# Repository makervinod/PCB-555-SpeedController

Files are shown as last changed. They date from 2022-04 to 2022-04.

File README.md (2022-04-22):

# 555 Speed Controller

## A 555 Timer-based Speed Controller for controlling DC Speed/Dimming

<br>

> This speed controller was purposely built for controlling the speed of Ender 3D Printer's Hotend Cooling Fan to help the hot-end support unofficial cooling fans. But it can be used for other purposes too! ( No limits to your use case! )

---

### Specifications:

- Operating Voltage: **12V to 24V**
- Maximum Output Current: **0.5 Amp (customizable)**

---

### Components Required:

| Sr. No. | Part Number/Name | Package  | Quantity | Description |
| --- | --- | --- | :---: | --- |
| 1 | NE555 | SOIC-8 | 1 | 555-Timer IC |
| 2 | 1N4742 | DO-41 | 1 | Diode (12V Zener, 1 Watt) |
| 3 | LL4148 (1N4148)  | MiniMELF | 2 | Diode |
| 4 | S8050 (J3Y) | SOT-23 | 1 | NPN Transistor |
| 5 | 22uF 50V | 1210 | 1 | Ceramic Capacitor |
| 6 | 0.1uF 16V | 0805 | 1 | Ceramic Capacitor |
| 7 | 0.01uF 16V | 0805 | 1 | Ceramic Capacitor |
| 8 | 560 Ω | 2512 | 2 | Resistor |
| 9 | 10 kΩ | 0805 | 1 | Resistor |
| 10 | 1 kΩ | 0805 | 1 | Resistor |
| 11 | 4.7 kΩ | 0805 | 1 | Resistor |
| 12 | 10 kΩ | Preset | 1 | Preset Potentiomenter |
| 13 | LED (Any color)  | 0805 | 1 | LED |

---

### Fabrication Notes:

1. This was built using the PCB Toner transfer process at home.
2. Use the `print` feature of KiCAD to print the PCB design according to your requirements.
3. I tinned the board using some normal solder wire & flux (budget-friendly)
4. Refer to the schematic to relate the placement of the components.

---

### Additional Notes:

> The circuit will dissipate high heat if operated beyond the specified rating. Choose an appropriate combination of the Zener diode & the heat-dissipating resistors to satisfy your requirements.

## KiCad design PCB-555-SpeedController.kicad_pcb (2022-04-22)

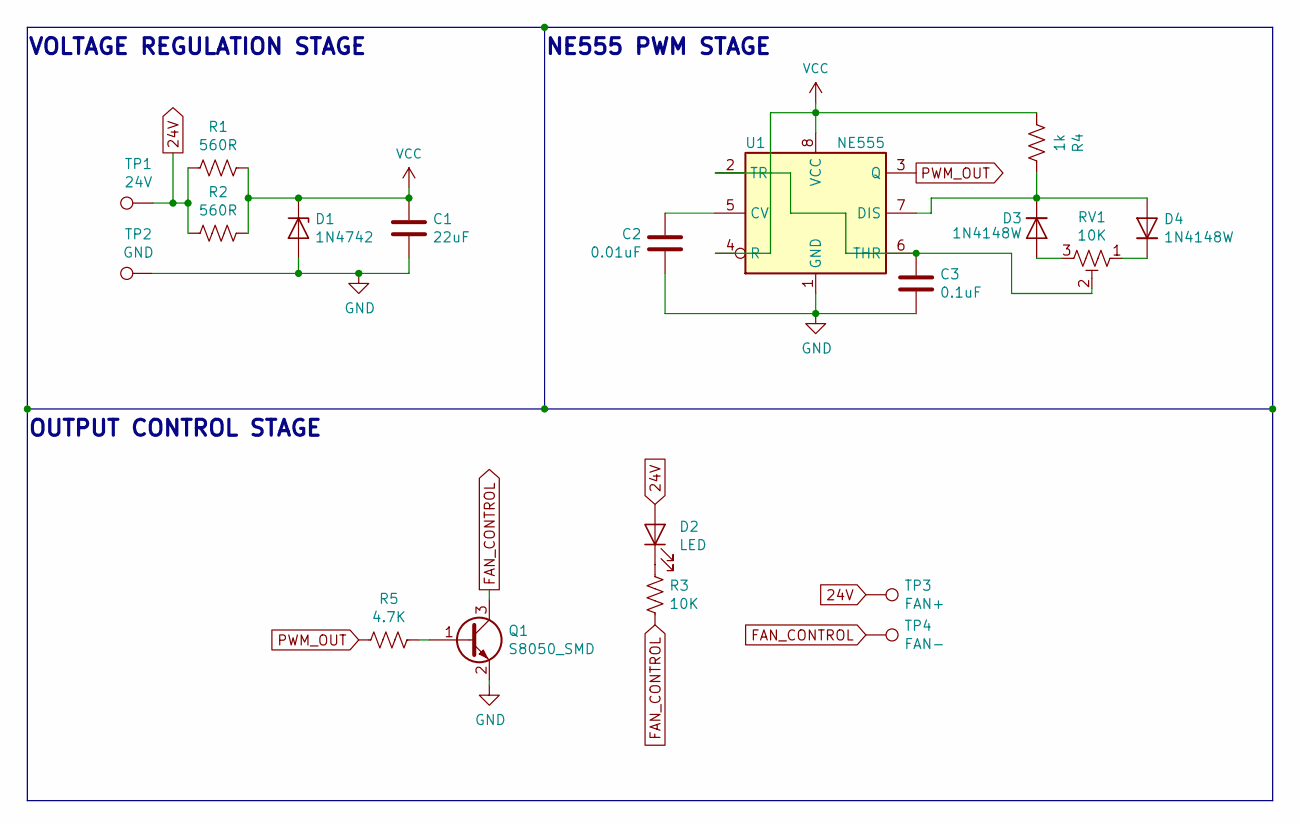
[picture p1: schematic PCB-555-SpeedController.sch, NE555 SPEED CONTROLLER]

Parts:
C1: 22uF; C_1210_3225Metric
C2: 0.01uF; C_0805_2012Metric
C3: 0.1uF; C_0805_2012Metric
D1: 1N4742; D_DO-41_SOD81_P10.16mm_Horizontal
D2: LED; LED_0805_2012Metric
D3, D4: 1N4148W; D_MiniMELF
Q1: S8050_SMD; SOT-23
R1, R2: 560R; R_2512_6332Metric
R3: 10K; R_0805_2012Metric
R4: 1k; R_0805_2012Metric
R5: 4.7K; R_0805_2012Metric
RV1: 10K; Potentiometer_Piher_PT-6-V_Vertical
TP1: 24V; TestPoint_Pad_2.0x2.0mm
TP2: GND; TestPoint_Pad_2.0x2.0mm
TP3: FAN+; TestPoint_Pad_2.0x2.0mm
TP4: FAN-; TestPoint_Pad_2.0x2.0mm
U1: NE555; SOIC-8_3.9x4.9mm_P1.27mm

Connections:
24V: D2.2 (A), R1.2, R2.2, TP1.1, TP3.1
FAN_CONTROL: Q1.3 (C), R3.1, TP4.1
GND: C1.2, C2.1, C3.2, D1.2 (A), Q1.2 (E), TP2.1, U1.1 (GND)
unnamed: C2.2, U1.5 (CV)
unnamed: C3.1, RV1.2, U1.2 (TR), U1.6 (THR)
unnamed: D2.1 (K), R3.2
unnamed: D3.1 (K), D4.2 (A), R4.1, U1.7 (DIS)
unnamed: D3.2 (A), RV1.3
unnamed: D4.1 (K), RV1.1
unnamed: Q1.1 (B), R5.1
PWM_OUT: R5.2, U1.3 (Q)
VCC: C1.1, D1.1 (K), R1.1, R2.1, R4.2, U1.4 (R), U1.8 (VCC)

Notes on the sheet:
OUTPUT CONTROL STAGE
NE555 PWM STAGE
VOLTAGE REGULATION STAGE

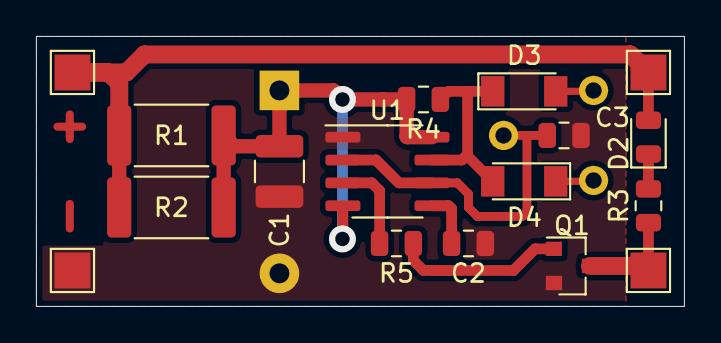
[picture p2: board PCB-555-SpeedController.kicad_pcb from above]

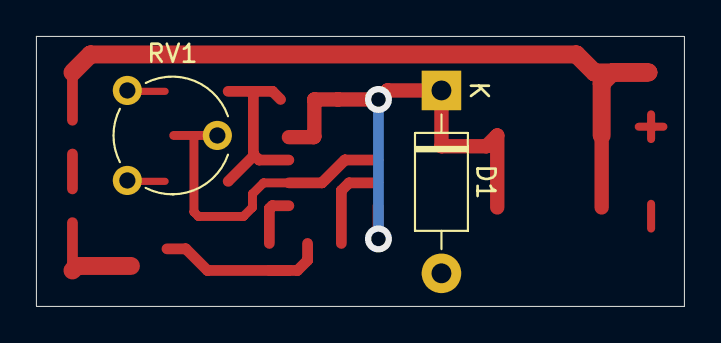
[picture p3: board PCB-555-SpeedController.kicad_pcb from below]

Board: 2 copper layers, 36.0 x 15.0 mm, 19 parts (2 on the bottom side), 12 nets.
